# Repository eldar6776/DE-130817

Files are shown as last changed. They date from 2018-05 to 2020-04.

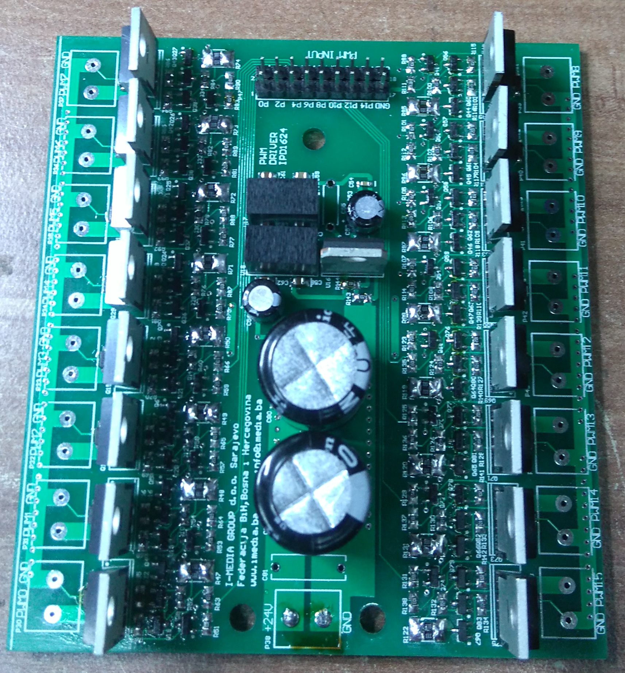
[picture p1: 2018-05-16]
RadioRxPwmImg3.JPG

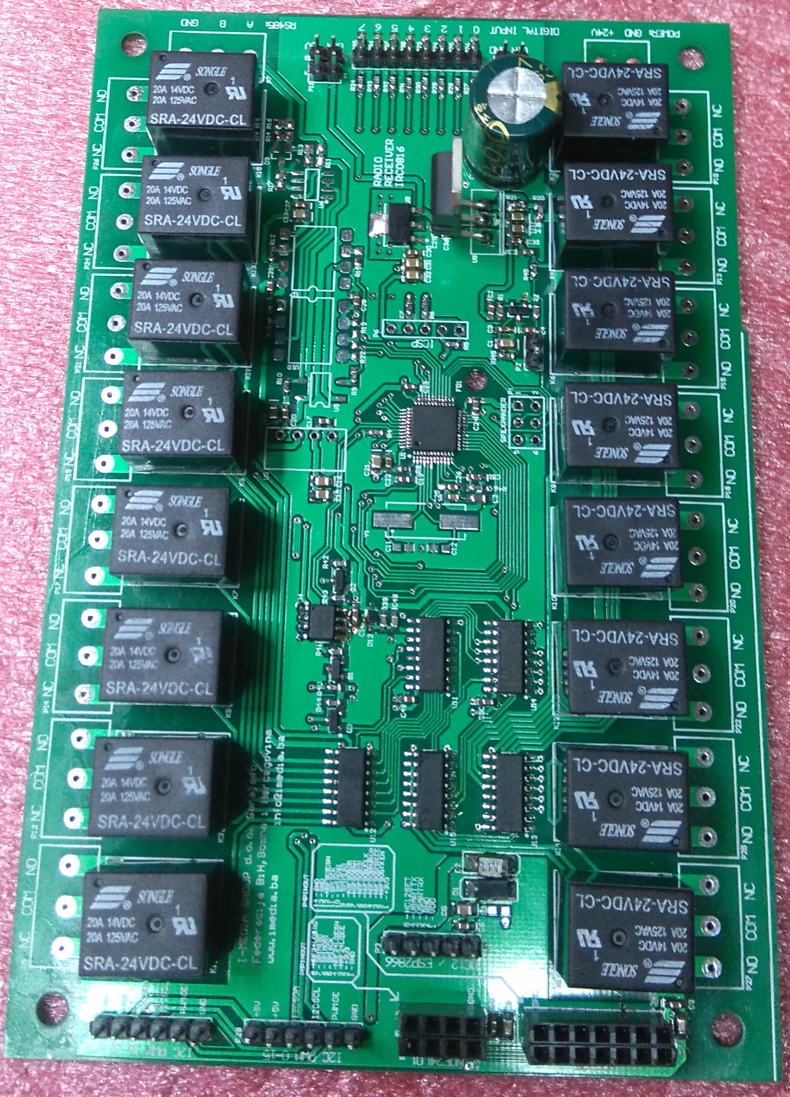
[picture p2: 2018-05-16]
RadioRxImg2.JPG

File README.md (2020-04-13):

# DE-130817
Two-Way Radio Link Receiver Modul

this is a receiver for DE-110817 transmitter, with a secure radio link to control the concrete pumps. 8 digital inputs are transmitted from the receiver to the transmitter, the PWM driver temperature of 65 degrees Celsius sends a warning to the transmitter, 80 degrees Celsius switches off and blocks the PWM and relay outputs except the oil pump and bypass valve controls. the supply voltage is also monitored. The 433MHz HC-12 radio modules are more than enough range for a stable radio link. if the transmitter does not confirm the transmitter packet longer than 500ms, the receiver switches off the outputs and an LED signal is activated on the transmitter.

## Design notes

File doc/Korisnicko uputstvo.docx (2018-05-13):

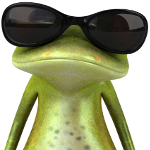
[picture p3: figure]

i MEDIA

__________________________________________________________________________________

Sistem radio kontrole pumpe za beton

Korisničko uputstvo

IRT0816 - Radio predajnik

8 analognih ulaza,

16 digitalnih ulaza,

8 led izlaza.

IRC0816 - Radio prijemnik

8 digitalnih ulaza,

16 relejnih izlaza,

16 PWM izlaza.

Posebne osobine:

- Podesiv indikator napona za većinu baterija ili akumulatora za napajanje predajnika: Nikal-Kadmium, suhi olovni akumulator, Litium-Ion, jednokratne alkalne baterije.
- Predupozorenje prazne baterije ispod 10% kapaciteta.
- Isključenje uređaja kod donjeg nivoa baterije što je ujedno i zaštita akumulatora od dubokog pražnjenja i oštećenja.
- Dvosmjerna radio komunikacija sa sigurnosnom funkcijom isključenja izlaza prijemnika kod prekida komunikacije >500 ms.
- Status prijemnika LED signalima na predajniku + stanje 8 digitalnih ulaza prijemnika koji se mogu koristiti za signalizaciju događaja sa prijemnika npr. min. nivou ulja, pregrijavanju, proradi zaštitnih uređaja, aktiviranju krajnjih ili sigurnosnih prekidača i sl.
- Stabilan izvor pozitivnog napona +3,3Vdc za referentni napon potenciometara spojenih na analogne ulaze.
- Zaštita PWM drivera od pregrijavanja sa signalom predupozorenja.
- RS485 interfejs za žičnu, backup, komunikaciju do 1km sa UTP, FTP, STP kablom za slučaj kvara ili smetnji radio komunikacije.

Fleksibilnost ugradnje:

- Jednostavno uspostavljanje optimalnog radio linka odabirom između 5 različitih radio modula i radnih frekvencija 315MHz, 433MHz, 868MHz, 915MHz, 2,4GHz, plug-and-play izmjenom bez dodatnih podešavanja za sigurnu radio kontrolu.
- Jednostavno podešavanje analognih ulaza za signale sa joystick potenciometara sa nulom na sredini klizača ili za signal potenciometara sa nulom signala na početku klizača
- Podesiva frekvencija PWM drivera za najoptimalniju kontrolu radnog uređaja sa što manjim gubicima i disipacijom temperature izlaznog PWM stepena.
- Mogućnost proširenja analognih/ digitalnih ulaza predajnika kao i pwm/relejnih izlaza prijemnika.
- Mogućnost ugradnje WiFi modula i kontrole prijemnika internet servisima tako da se modul može kristiti u Smart Home sistemu za on/off kontrolu 16~32 potrošača. PWM driver se bez ikakve preinake može koristiti za dimmer kontrolu 5~10 RGB ili 16~32 White LED nizova velike snage. Sa malim izmjenama, t.j. zamjenom tri komponente po kanalu, PWM driver se može transformisat u 16~32 kanalni DAC kojim se generišu kontrolni signali 0~10Vdc, a koji su industrijski standard i ulazni kontrolni signal kod mnogih LED dimmera

Karakteristike periferija:

- Signal na digitalnom ulazu prijemnika ili predajnika < 1Vdc je stanje logičke nule.
- Signal na digitalnom ulazu prijemnika ili predajnika > 2Vdc je stanje logičke jedinice.
- Maximalan pozitivni napon digitalnih ulaza prijemnika ili predajnika je < 30Vdc.
- Maksimalan pozitivni napon analognih ulaza predajnika je < 3,6Vdc.
- Signal na ulazu PWM drivera > 4Vdc postavlja izlaz PWM-a na visoki nivo (napon napajanja PWM drivera).
- Signal na ulazu PWM drivera < 3,5 Vdc postavlja izlaz PWM-a na niski nivo (GND PWM drivera).
- Izlaz PWM-a je N-MOSFET, zbog manjih gubitaka, u high-side switch spoju, t.j. kontrola pozitivnog napona. Upotrebljeni tip je maksimalnog radnog napona 100Vdc i 20A konstantne struje pri temperaturi kućišta do 100°C.
- Za temperature hladnjaka PWM drivera > 65°C aktivira se signal upozorenja na prijemniku.
- Temperatura hladnjaka PWM drivera > 80°C aktivira signal preopterećenja na prijemniku i aktivira zaštitnu funkciju koja isključuje sve izlaze prijemnika i onemogućava aktiviranje dok temperatura hladnjaka ne opadne ispod 65°C.
- Temperaturni senzor temperature hladnjaka PWM-a je NTC otpornik otpora 10K na temperaturi 25°C, na temperaturi 65°C je 2 K, a na temperaturi 80°C je 1,25 K.
- Na svim analognim ulazima su ugrađeni niskopropusni RC filteri ~150Hz koji eliminišu ili uveliko umanjuju smetnje nastale pomjeranjem klizača potenciometara koji su pred kraj radnog vijeka ili su već istrošeni.

Sadržaj uputstva:

1.0 Podešavanje i upotreba modula predajnika ................................... 6
2.0 Podešavanje i upotreba modula prijemnika.................................... 12
3.0 Pregled modula PWM drivera............................................................... 14
4.0 Električne sheme ......................................................................................... 17
5.0 Održavanje uređaja ................................................................................... 19
1. Podešavanje i upotreba modula predajnika :

raspored i namjena konektora na modulu radio predajnika

Kontrolni

taster

Konektor za

signalne LED

Konektor za

RS485 bus

Konektor za

napajanje

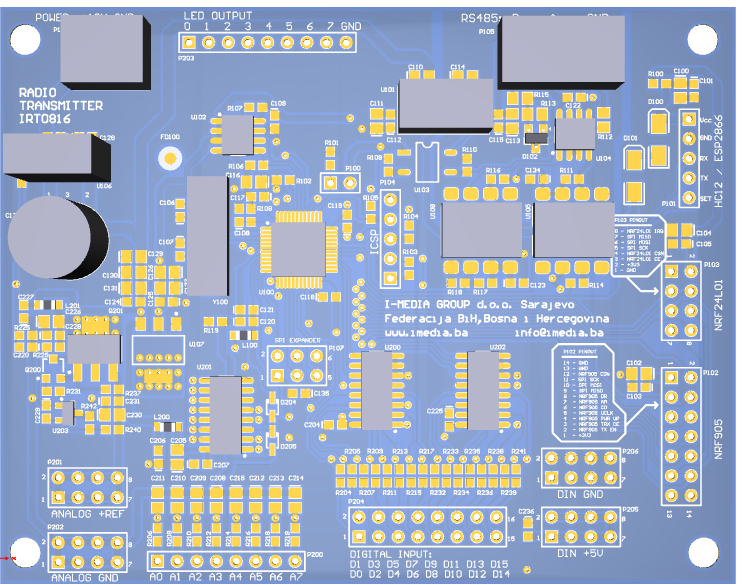
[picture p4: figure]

Konektor za modul proširenja

Konektor za

HC12 radio

modul i WiFi

Konektor za

NRF24L01

radio modul

Konektor za

NRF905 radio

modul

Masa za potenciometre

+3,3Vdc za

potenciometre

Analogni ulazi za potenciometre

Digitalni

ulazi

Masa za digitalne ulaze

+5Vdc za

digitalne ulaze

tabela napona standardnih ćelija

Tip ćelije/ napon | Olovna | Ni-Cd | Ni-MH | Li-ion
Napon ćelije (nominal.) | 2V | 1,2V | 1,2V | 3,7V
Napon pune ćelije | 2,40V | 1,45V | 1,41V | 4,20V
Napon prazne ćelije | 1,75V | 1,00V | 1,00V | 3,20~3,40V

  1.1 Način aktiviranja i izlaz iz funkcije podešavanja

Funkcija za podešavanje modula se aktivira tako da se pritisne kontrolni taster,

a zatim dok je taster pritisnut priključi napajanje predajnika. Sve statusne LED kratkim signalom označavaju da je funkcija aktivna. Nakon što je definisan parametar koji se podešava potrebno je kratko pritisnut kontrolni taster čime se nova vrijednost memoriše u eeprom i odmah je validna. Statusne LED sa tri kratka signala označavaju izlaz iz funkcije za podešavanje.

  1.2 Definisanje analognih ulaza

Kada je digitalni ulaz D0 spojen na +5Vdc i svi ostali digitalni ulazi su slobodni ili spojeni na masu, aktivirana funkcija podešavanja se odnosi na definisanje tipa signala na analognim ulazima. Analogne ulaze na koje će u toku rada uređaja biti spojen signal sa joystick potenciometra treba spojiti na 3,3Vdc, a analogne ulaze koji na koje će biti spojen signal sa standardnog potenciometra treba spojiti na masu. Nakon izlaza iz funkcije podešavanja definisani su analogni ulazi. Veoma je bitno da se ima u vidu da će sve promjene prvom konekcijom biti podešene i na prijemniku. Analogni ulaz predajnika na koji je spojen signal potenciometra joystick-a, na strani prijemnika kontroliše dva PWM izlaza koji su uvijek susjedni, a signal standardnog potenciometra kontroliše jedan PWM. Kada se promjeni definicija analognih ulaza treba i na strani prijemnika utvrditi novi raspored PWM izlaza.

  1.3 Podešavanje napona prazne baterije

Kada je digitalni ulaz D1 predajnika spojen na +5Vdc i svi ostali digitalni ulazi su slobodni ili spojeni na masu, aktivirana funkcija podešavanja se odnosi na definisanje napona prazne baterije. Napon napajanja treba podesiti na napon prazne baterij, a što se može izračunati prema „tabeli napona standardnih ćelija“, tako da se pomnoži broj članaka u bateriji za napajanja sa naponom prazne ćelije za korišteni tip. Najbolje je za napajanje koristiti podesivi izvor istosmjernog napona, a može se koristiti i ispražnjena baterij. Kada je napon definisan, kratko pritisnut kontrolni taster čime je izmjerena vrijednost memorisana kao donji prag napona baterije.

  1.4 Podešavanje napona pune baterije

Kada je digitalni ulaz D2 predajnika spojen na +5Vdc i svi ostali digitalni ulazi su slobodni ili spojeni na masu, aktivirana funkcija se odnosi na podešavanje napona pune baterije. Napon napajanja treba prije podesiti na napon pune baterije, a što se može izračunati prema „tabeli napona standardnih ćelija“, tako da se pomnoži broj članaka u bateriji za napajanja sa naponom pune ćelije za korišteni tip. Najbolje je za napajanje koristiti podesivi izvor istosmjernog napona, a može se koristiti i puna baterija. Kada je napon definisan, potrebno je kratko pritisnut kontrolni taster čime je izmjerena vrijednost memorisana kao napon pune baterije.

  1.5 Podešavanje frekvencije PWM izlaza 0 ~ 15

Kada je digitalni ulaz D3 predajnika spojen na +5Vdc i svi ostali digitalni ulazi su slobodni ili spojeni na masu, aktivirana je funkcija podešavanja frekvencije PWM signala za izlaze od 0 ~ 15. Signalom od 0 do 3,3Vdc na analognom ulazu A0 predajnika se podešava frekvencija PWM izlaza na prijemniku u rasponu od 24Hz do1526Hz. LED signali predstavljaju podešenu vrijednost i to za svaki LED koji svijetli konstantno frkvencija se uvećava za 200Hz, a trepćući signal označava uvećanje za 100Hz. Podešena frekvencija će biti podešena na prijemniku kod prve radio komunikacije sa predajnikom.

  1.6 Podešavanje frekvencije PWM izlaza 16 ~ 31

Kada je digitalni ulaz D4 predajnika spojen na +5Vdc i svi ostali digitalni ulazi su slobodni ili spojeni na masu, aktivirana je funkcija podešavanja frekvencije PWM signala za izlaze od 16 ~ 31. Signalom od 0 do 3,3Vdc na analognom ulazu A0 predajnika se podešava frekvencija PWM izlaza na prijemniku u rasponu od 24Hz do1526Hz. LED signali predstavljaju podešenu vrijednost i to za svaki LED koji svijetli konstantno frkvencija se uvećava za 200Hz, a trepćući signal označava uvećanje za 100Hz. Podešena frekvencija će biti podešena na prijemniku kod prve radio komunikacije sa predajnikom.

  1.7 Provjera statusa baterije

Kratkim pritiskom na kontrolni taster modula predajnika provjerava se status baterije prema LED signalima u rasponu od LED 0 za najmanji nivo do LED 7 za punu bateriju. Nakon 5 sekundi LED signali ponovo označavaju status prijemnika.

  1.8 Provjera statusa radio linka

Kratkim pritiskom na kontrolni taster modula predajnika za vrijeme provjere statusa baterije aktivira se provjera kvaliteta radio linka prema LED signalima u rasponu od LED 0 do LED 7. Ovaj mod ostaje aktivan do novog ciklusa napajanja

ili sledećeg pritiska na kontrolni taster nakon čega se ponovo LED signalima označava status prijemnika. Mjerenjem kvaliteta radio linka se mogu na vrijeme uočiti zone lošeg radio signala i izbjeći zastoji u radu mašine.

  1.9 Nuliranje analognih ulaza

Dužim pritiskom > 3s kontrolnog tastera modula predajnika, kada nije aktivna ni jedna druga funkcija podešavanja ili provjere, te otpuštanjem kontrolnog tastera, signali na analognim ulazima se definišu kao nulte pozicije potenciometara. Prije poziva ove funkcije potrebno je sve potenciometre dovesti u početne ili neutralne pozicije. Za potenciometre joystick-a napon signala u neutralnom položaju je idealno 1,65Vdc, a za ostale potenciometre je napon signala u početnoj poziciji 0Vdc, mada se ovom funkcijom mogu definisati nulte pozicije potenciometara i u bilo kojem drugom položaju npr. kada je signal sa potrošenog potenciometra nestabilan (šušti) na početku hoda, može se nula pomjeriti na dio klizača odakle je signal stabilan. Sve vrijednosti ispod nulte pozicije klizača su jednake nuli signala na izlazu PWM-a.

  1.10 RS485 interfejs za serijsku - backup konekciju

Komunikaciju između predajnika i prijemnika je moguće ostvariti povezivanjem RS485 interfejsa predajnika i prijemnika uvrnutom paricom dužine do 1000 m. Brzina serijske komunikacije je 9600 bps, a format 8-N-1. Ovim interfejsom se korištenjem seta komandi mogu podesiti svi parametri prijemnika i predajnika. Potreban je serijski teminal softver (npr. realterm) i konverter USB/RS485.

  1.11 HC-12 Radio modul

Radna frekvencija je u opsegu 433 – 473MHz podjeljena na 100 kanala. Uz izlaznu snagu od max. 100mW (20dB) i brzinu prenosa do 5000 bps na otvorenom prostoru moguće je ostvariti dvosmjernu komunikaciju do 1000 m. Ako je par ovih radio modula priključen na konektore P3 prijemnika i P101 predajnika, u toku inicijalizacije softvera prvi su odabir za radio link.

  1.12 NRF24L01+PA+LNA Radio modul

Radna frekvencija je 2,4GHz. Izlazna snaga predajnika je >100mW (>20dB), brzina prenosa do 2MB. Na otvorenom prostoru moguće je ostvariti dvosmjernu komunikaciju preko 700 m, brzine prijenosa 1MB. Ako je par ovih radio modula priključen na konektore P5 prijemnika i P103 predajnika, u toku inicijalizacije softvera drugi su odabir za radio link.

  1.13 NRF905 Radio modul

Radne frekvencije su u tri banda 433/868/915MHz. Izlazna snaga predajnika je 10mW (10dB) , brzina prenosa do 50 kbps. Na otvorenom prostoru moguće je ostvariti dvosmjernu komunikaciju do 300 m. Ako je par ovih radio modula priključen na konektore P4 prijemnika i P102 predajnika, u toku inicijalizacije softvera treći su odabir za radio link uspostavljen na bandu 433MHz.

  1.14 LED signalizacija stanja digitalnih ulaza prijemnika i greške

Konektor P203 modula predajnika omogućava monitoring raznih statusa prijemnika i predajnika sa 8 LED dioda koje se spajaju anodama na pinove 1 do 8 konektora P203, a sve katode se spajaju na zajednički pin 9. Serijski otpornici su ugrađeni na modulu i nije ih potrebno dodavati eksterno. Struja izlaza za LED diode sa padom napona od 2V je ~3mA, a za LED diode sa padom napona 3V je ~1mA, što treba uzeti u obzir kada se uređaj napaja baterijama.

Stanje aktivnog digitalnog ulaza na prijemniku se signalizira konstantno svjetlećom LED na predajniku sa istim brojem (LED 0 za digitalni ulaz DIN 0) i obratno, LED je neaktivna kada je digitalni ulaz neaktivan.

Signalizacija greške se označava sa tri kratke promjene stanja LED signala i pauzom od tri sekunde. To znači ako LED svijetli zato što je taj digitalni ulaz aktivan, onda će emitovanje svjetla biti tri puta kratko prekinuto i nakon svake tri sekunde ponovo, a ako je LED bila neaktivna onda će tri puta kratko zasvjetliti i nakon tri sekunde pauze ponavljati ovaj signal.

Značenje signaliziranih grešaka:

LED 0 - napon baterije za napajanje predajnika ispod 10% - upozorenje

LED 1 - baterija za napajanje predajnika prazna - isključenje

LED 2 - greška modula I2C PWM kontrolera - isključenje

LED 3 - temperatura hladnjaka PWM izlaza veća od 65°C - upozorenje

LED 4 - temperatura hladnjaka PWM izlaza veća od 80°C - isključenje

LED 5 - greška NTC temistora za mjerenje temperature PWM - isključenje

LED 6 - prekid radio linka > 500 ms - isključenje

LED 7 - prekid u napajanju prijemnika - isključenje

  1.15 Spajanje analognih ulaza

Svi analogni ulazi su za napone od 0 do 3,3Vdc (!!! NE 5Vdc), za što je na PCB-u modula preajnika obezbjeđen stabilan referentni izvor napona na konektoru P201. Potenciometri na ulazu se spajaju na konektore P200, P201 i P202.

ANALOG +REF (P201)

A0; A1....A7 (P200)

ANALOG GND (P202)

  1.16 Spajanje digitalnih ulaza

Svi digitalni ulazi su predviđeni za ulazni napon do 30Vdc. Na PCB-u modula predajnika se nalaze konektori P204; P205; P206 za dva načina spajanje digitalnih ulaza: sa eksternim izvorom i internim izvorom. Kod spajanja sa internim izvorom, na konektoru P205 je obezbjeđen izvor +5Vdc za beznaponski kontakt koji se drugim izvodom spaja na digitalne ulaze na konektoru P204. Ako se koristi eksterni izvor, minus pol izvora se spaja na DIN GND konektor P206 modula, a pozitivan pol izvora se spaja na digitalne ulaze na konektoru P204. Stanje digitalnog ulaza u odnosu na napon izvora je opisano u dijelu „Karakteristike periferija“.

spajanje digitalnog ulaza za internim izvorom

DIN +5V(P205) D0; D1.....D15 (P204)

spajanje digitalnog ulaza za eksternim izvorom

0~30V D0; D1.....D15 (P204)

GND DIN GND(P206)

  1.17 Spajanje kontrolnog tastera

Za korištenje funkcija: „provjera statusa baterije, provjera statusa radio linka, nuliranje analognih ulaza “, kao i za podešavanja modula predajnika potreban je spoj kontrolnog tastera. Ovaj taster bi trebao biti zaštićen od slučajnog pritiska u toku rada sa predajnikom zbog mogućnosti neželjenog aktiviranja funkcije „nuliranje analognih ulaza“ , a samim tim i zastoja u radu dok se ova funcija ponovo provede.

spajanje kontrolnog tastera

P100/1 P100/2

2. Podešavanje i upotreba modula prijemnika :

raspored i namjena konektora na modulu radio predajnika

LOOP VENTIL

RELEJ 15

RELEJ 9

RELEJ 10

RELEJ 11

RELEJ 12

RELEJ 13

RELEJ 13

RELEJ 14

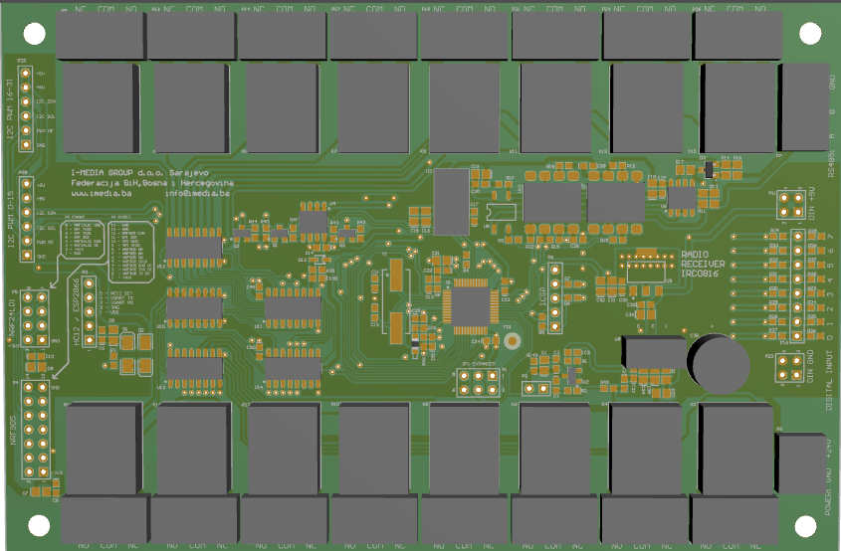
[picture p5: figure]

Konektor NTC senzora

Masa za digitalne ulaze

Konektor za

napajanje

RELEJ 7

RELEJ 6

RELEJ 5

RELEJ 8

RELEJ 4

RELEJ 3

RELEJ 2

RELEJ 1

Konektor za

NRF905

radio modul

Konektor za

PWM kontroler 2

modul

Konektor za

RS485 bus

Digitalni

ulazi

+5Vdc za

digitalne ulaze

Konektor za

NRF24L01

radio modul

Konektor za

PWM kontroler 1

modul

Konektor za

HC12 radio

modul i WiFi

  2.1 NTC senzor temperature hladnjaka PWM izlaza

Tip NTC senzora je pisan u dijelu „Karakteristike periferija“ i korišten je veoma dostupan i najčešće korišteni tip 10K na 25°C. Kada se koristi potrebno je tijelo NTC termistora sa malo termoprovodne paste učvrstiti na hladnjak PWM izlaza i dvožičnim provodnikom spojiti na P2 modula prijemnika. Ovaj provodnik je potrebno odvojiti od provodnika PWM i relejnih izlaza koji su izvor smetnji.

Monitoring teperature hladnjaka PWM drajvera se može isključiti postavljanjem jumpera (kratak spoj) na konektor P2 u slučaju npr. neispravnog NTC termistora ili kada se ne koristi PWM driver.

  2.2 Spajanje digitalnih ulaza

Svi digitalni ulazi su predviđeni za ulazni napon do 30Vdc. Na PCB-u modula prijemnika se nalaze konektori P11; P16; P23 za dva načina spajanje digitalnih ulaza: sa eksternim izvorom i internim izvorom. Kod spajanja sa internim izvorom, na konektoru P11 je obezbjeđen izvor +5Vdc za beznaponski kontakt koji se drugim izvodom spaja na digitalne ulaze na konektoru P16. Ako se koristi eksterni izvor, minus pol izvora se spaja na DIN GND konektor P23 modula, a pozitivan pol izvora se spaja na digitalne ulaze na konektoru P16. Stanje digitalnog ulaza u odnosu na napon izvora je opisano u dijelu „Karakteristike periferija“.

spajanje digitalnog ulaza za internim izvorom

DIN +5V(P11) D0; D1.....D7 (P16)

spajanje digitalnog ulaza za eksternim izvorom

0~30V D0; D1.....D7 (P16)

GND DIN GND(P23)

  2.3 Spajanje PWM kontrolera

Na modul prijemnika je moguće priključiti dva 16 kanalna PWM kontrolera za generisanje PWM signala 0-5Vdc. Kada se koristi drugi PWM kontroler, na prijemniku je potrebno ugraditi modul proširenja analognih ulaza. Rad modula prijemnika je moguć sa i bez modula PWM kontrolera. Ako je modul PWM kontrolera priključen na PCB prijemnika, nakon priključenja napona, softver će registrovati modul i u slučaju kvara ili isključenja u toku rada prijavit će grešku modula te isključiti sve izlaze prijemnika. Ako modul PWM kontrolera nije bio priključen kod uključenja napajanja prijemnika, PWM funkcija izlaza se ne koristi te prijemnik služi kao on/off rejeni kontroler.

Pregled modula PWM drivera :

PCB i raspored komponenti PWM Drivera IPD1624

PWM

izlaz 5

PWM

izlaz 4

PWM

izlaz 3

PWM

izlaz 2

PWM

izlaz 1

PWM

izlaz 0

PWM

izlaz 7

PWM

izlaz 6

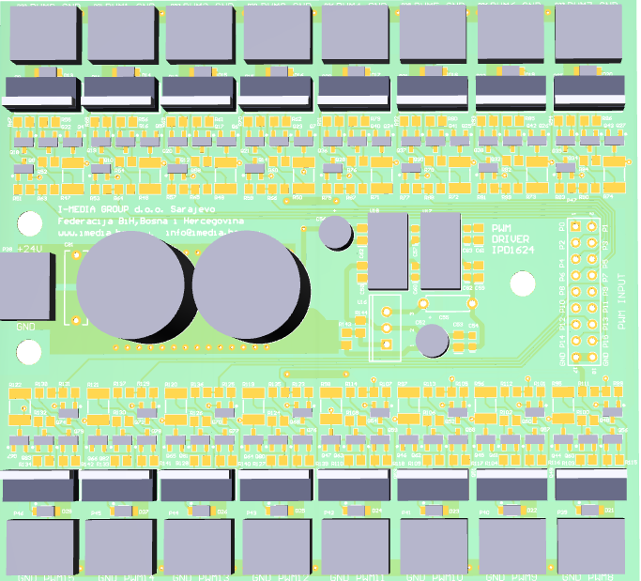
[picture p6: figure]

PWM

izlaz 9

PWM

izlaz 10

PWM

izlaz 11

PWM

izlaz 12

PWM

izlaz 13

PWM

izlaz 14

PWM

izlaz 15

Napajanje

PWM

drivera

PWM

ulazi

0 ~ 15

PWM

izlaz 8

PWM driver IPD1624 je predviđen kao univerzalan PWM izlazni stepen za širok opseg opterećenja i radnih napona, te kao takav nema implementiranu prekostrujnu zaštitu i koju je potrebno izvesti eksterno prema opterećenju koje se spaja na izlaz. Zaštita se može izvesti serijskom vezom staklenog rastalnog osigurača (tromog T ili brzog F) i priključenog opterećenja t.j. radnog uređaja (proporcionalni elektro ventil, servo pozicioner, aktuator), a što treba provjeriti u specifikaciji za taj uređaj. Primjer spoja zaštite je skiciran ispod.

SF52 (5A, 100V)

ventil

T2A

PWM GND

izlaz osigurač

Niti na jedan od PWM izlaza drivera se ne smije priključivati izvor napajanja bilo da je PWM driver priključen na napajanje ili da je napajanje isključeno. Ovo bi za posljedicu imalo pregorijevanje gate otpornika izlaznog MOSFET-a, zaštitne zener diode ili pnp gate-driver tranzistora.

Ukoliko je potreban bilo kakav paralelan rad PWM drivera i nekog drugog kontrolnog sklopa, potrebno je ili napraviti preklopnik ručna komanda – radio komada ili na izlaz PWM-a koji je u paralelnom spoju sa dodatnom kontrolom ugraditi diodu za blokadu pozitivnog napona sa izlaza prema unutrašnjem sklopu PWM drivera. Dioda treba biti dimenzionisana prema struji priključenog opterećenja. Treba voditi računa da je pad napona na diodi oko 0,5 V što uz veću struju opterećenja od npr. 2A daje disipaciju od 1W, tako da je potrebno pobrinuti se za odvođenje viška toplote sa diode na hladnjak .

spoj za preklopnik ručna komanda – radio komada

SF52 (5A, 100V)

PWM

T2A

izlaz

ventil

GND

Ručna

komanda

relej

Odabir

kontrole

spoj za blokadu pozitivnog napona sa ručne kontrole prema PWM driveru

MBRF20100CT SF52 (5A, 100V)

ventil

T2A

PWM

izlaz

GND

Ručna

komanda

Na sva induktivna opterećenja kontrolisana PWM driverom koja nemaju ugrađen snubber, obavezno je ugraditi flyback diodu bar duplo veće struje od struje kontrolisanog induktiviteta i bar duplo većeg reversnog napona od napona napajanja PWM drivera. Bez eliminisanja smetnji koje nastaju kod isključenja napajanja induktivitetu, moguća su spontana, nekontrolisana uključenja izlaza PWM drivera kao i nekontrolisani reseti mikrokontrolera.

spoj flyback - zaštitne diode na induktivno opterećenje (elektroventil 2A, 24Vdc)

SF52 (5A, 100V)

T3,15A

ventil

PWM GND

izlaz

Električne sheme :

spajanje modula PWM kontrolera, PWM izlaza i radio modula prijemnika

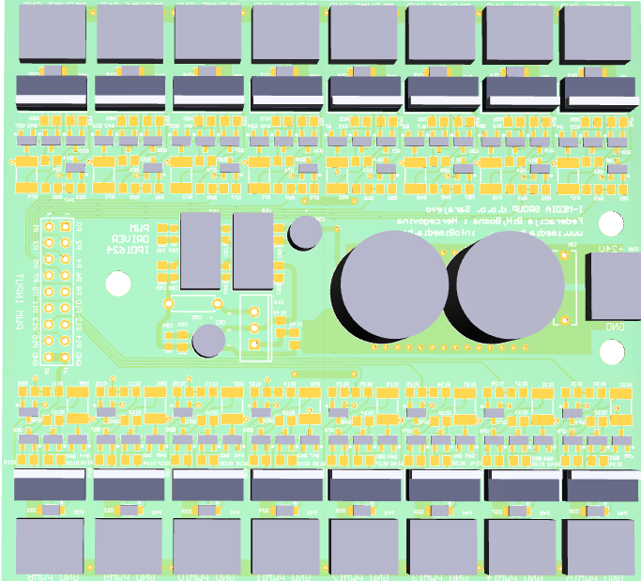
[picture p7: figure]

HC12

radio modul

vcc

PWM kontroler

!!! Kod povezivanja modula obrati pažnju na crveni marker kabla.

spajanje radio modula predajnika

HC12

radio modul

vcc

!!! Kod povezivanja modula obrati pažnju na crveni marker kabla.

Održavanje uređaja:

Ukoliko je signal sa potenciometra do te mjere nestabilan da prolazi kroz RC filter analognih ulaza, može se (za prvu pomoć) između signala sa klizača potenciometra i mase spojiti kondenzator 10 ~47 uF/10V pazeći da se negativni pol kondenzatora spoji na masu, a pozitivni na klizač. Veći kapacitet kondenzatora ima za rezultat veću stabilnost signala ali ujedno i sporiji odziv na promjene položaja potenciometra. Naročito je važno kašnjenje do nule signala t.j. kada se klizač brzo pomjeri u nultu poziciju, signal će kasniti i još neko vrijeme ostati aktivan dok ne postigne nultu vrijednost, pa je najbolje potenciometre koji uzrokuju smetnje zamjeniti novim.

BETTON PLANET © 2007–2018 I-Media Group d.o.o SarajevoPage 15

IRT0816 – Radio transmiter & IRC0816 – Radio receiver

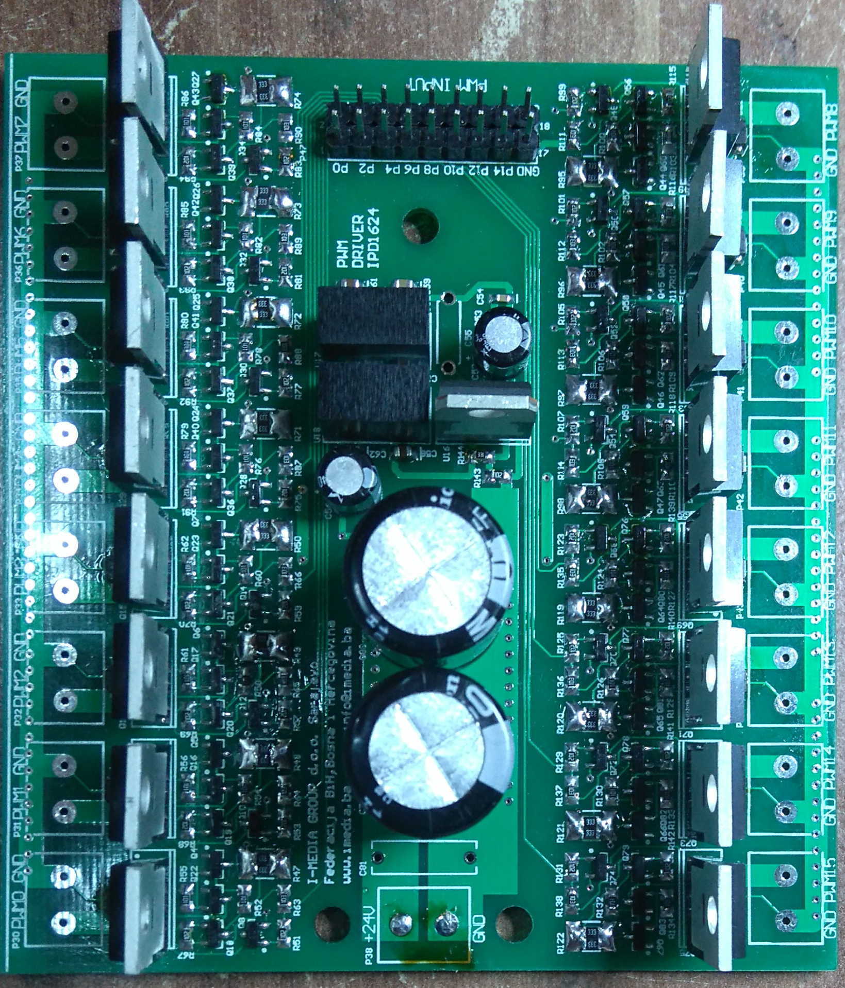
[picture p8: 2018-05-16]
RadioRxPwmImg1.JPG

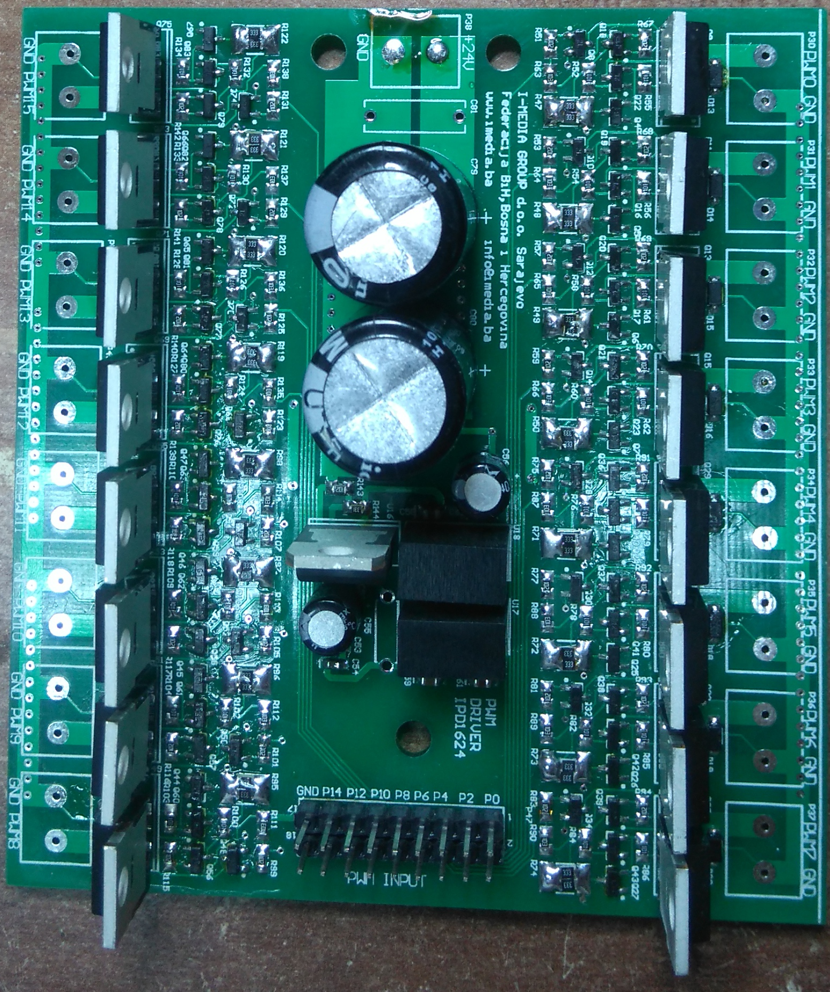
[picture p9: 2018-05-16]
RadioRxPwmImg4.JPG

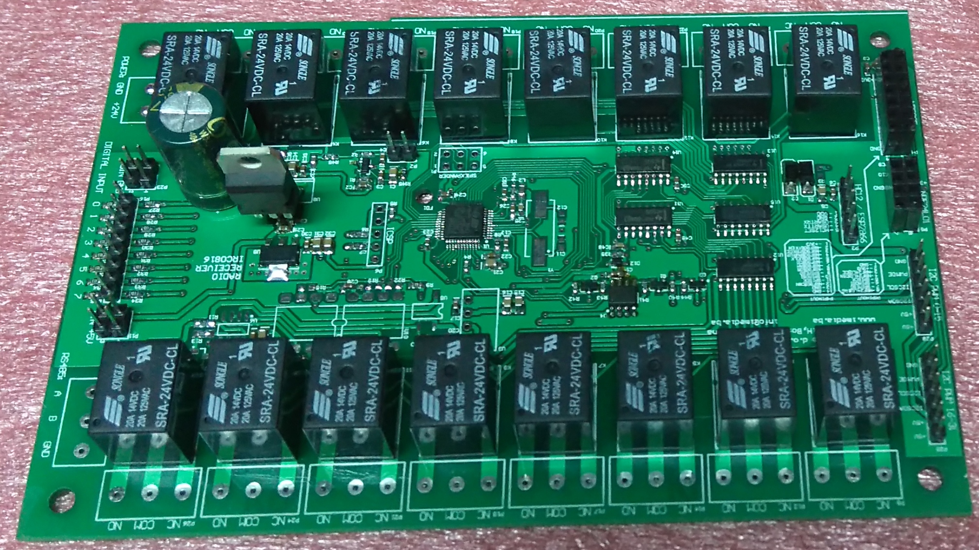
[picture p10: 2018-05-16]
RadioRxImg1.JPG

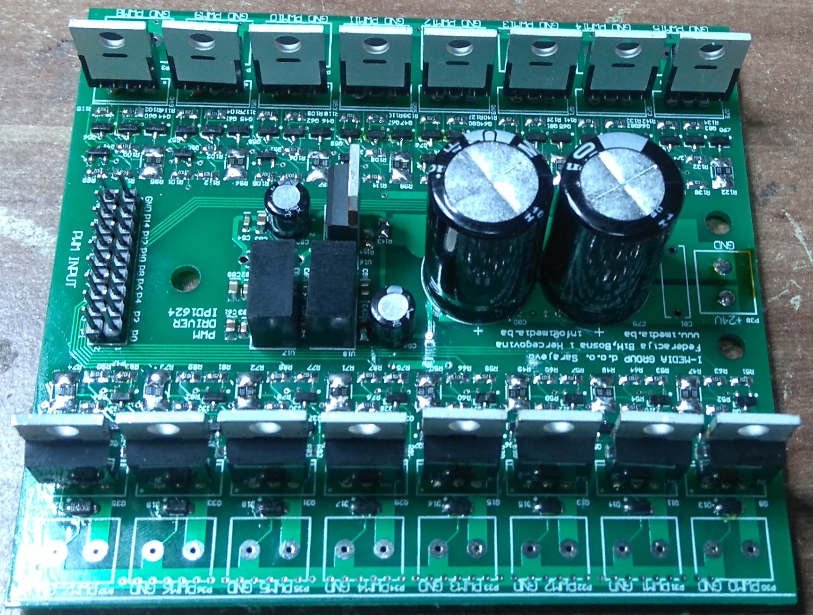
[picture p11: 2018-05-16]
RadioRxPwmImg2.JPG

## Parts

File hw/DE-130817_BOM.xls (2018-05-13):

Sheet: BOM Report
Bill of Materials |  |  | Cuc & Com
Source Data From: |  | DE-130817.PrjPcb
Project: |  | DE-130817.PrjPcb
Variant: |  | None
Creation Date: | 13.5.2018. | 14:30:54
Print Date: | 43233 | 43233.60602
Footprint | Comment | LibRef | Designator | Description | Quantity
0805 | 10uF | C0805 | C1, C5, C7, C9, C15, C16, C18, C19, C21, C31, C32, C34, C35, C36, C53, C58, C59, C61, C62 | Ceramic Chip Capacitor - Standard | 19
0603 | 100nF | C0603 | C2, C3, C4, C6, C8, C10, C13, C14, C17, C20, C22, C23, C24, C26, C27, C28, C29, C30, C33, C37, C39, C40, C41, C42, C43, C44, C45, C46, C47, C49, C50, C51, C54, C57, C60, C82, C83 | Ceramic Chip Capacitor - Standard | 37
0603 | 22pF | C0603 | C11, C12 | Ceramic Chip Capacitor - Standard | 2
0603 | 1uF | C0603 | C25, C48 | Ceramic Chip Capacitor - Standard | 2
CAPPR5-10x16 | 1000uF | EKA00DD410D00 | C38 | Aluminum Electrolytic Capacitor, Radial Style with Long Leads: 1000uF, 16V | 1
CAPPR2-5X11 | EKA00AA247F00 | EKA00AA247F00 | C52, C56 | Aluminum Electrolytic Capacitor, Radial Style with Long Leads: 47uF, 35V | 2
VP52-2.5 | VP52BY104 | VP52BY104 | C55 | Dipped Radial Multilayer Ceramic Capacitor X7R: 100nF | 1
CAPPR7.5-16X35.5 | EKA00JL422H00 | EKA00JL422H00 | C79, C80 | Aluminum Electrolytic Capacitor, Radial Style with Long Leads: 2200uF, 50V | 2
VP60-3.6 | VP60BA104FB | VP60BA104FB | C81 | Dipped Radial Multilayer Ceramic Capacitor COG (NPO): 100nF, 100V | 1
SMA | 1N4001 | 1N4001 | D1, D2 | Schottky Rectifier | 2
SOT23_3L | SM712 | 824022 | D3 | TVS Diode WE-TVS-Standard, VRWM=5.0V | 1
ONSC-SOD-323-2-477-02_V | 3V3 | MM3Z33VT1G | D4, D5, D6, D7, D8, D9, D10, D11 | Zener Voltage Regulator, 300 mW, 2-Pin SOD-323, Pb-Free, Tape and Reel | 8
SOD323 | 1N4148 | BAS321 | D12 | General-purpose Diode | 1
ONSC-SOD-123-2-425-04_V | SZMMSZ12T1G | SZMMSZ12T1G | D13, D14, D15, D16, D17, D18, D19, D20, D21, D22, D23, D24, D25, D26, D27, D28 | Zener Voltage Regulator, 500 mW, 2-Pin SOD-123, Pb-Free, Tape and Reel | 16
SRA-5VDC-CL | SRA-5VDC-CL | SRA-5VDC-CL | K1, K2, K3, K4, K5, K6, K7, K8, K9, K10, K11, K12, K13, K14, K15, K16 | SPDT PCB relay 5Vdc coil | 16
SMD-0805 | 120R | 74279202 | L2 | SMD EMI Suppression Ferrite Bead WE-CBF, Z = 120 Ohm | 1
HDR2X3 | SPI2_EXP | Header 3X2 | P1 | Header, 3-Pin, Dual row | 1
HDR1X2 | 10K NTC | Header 2 | P2 | Header, 2-Pin | 1
HDR1X5 | HC12_RADIO | Header 5 | P3 | Header, 5-Pin | 1
HDR2X7 | nRF905 | Header 7X2 | P4 | Header, 7-Pin, Dual row | 1
HDR2X4 | NRF24L01 | Header 4X2 | P5 | Header, 4-Pin, Dual row | 1
HDR1X5 | ULINK_ICSP | Header 5 | P6 | Header, 5-Pin | 1
TERMINAL BLOK 3 | TERMINAL BLOK 3 | TERMINAL BLOK 3 | P7, P9, P10, P12, P13, P14, P15, P17, P18, P19, P20, P21, P22, P24, P25, P26, P27 | 3 pinski terminal blok konektor | 17
TERMINAL BLOK 2 | TERMINAL BLOK 2 | TERMINAL BLOK 2 | P8, P30, P31, P32, P33, P34, P35, P36, P37, P38, P39, P40, P41, P42, P43, P44, P45, P46 | 2 pinski terminal blok | 18
HDR2X2 | DIN_VCC | Header 2X2 | P11 | Header, 2-Pin, Dual row | 1
HDR1X8 | DIGITAL_INPUT | Header 8 | P16 | Header, 8-Pin | 1
HDR2X2 | DIN_VSS | Header 2X2 | P23 | Header, 2-Pin, Dual row | 1
HDR1X6 | I2C_PWM_0_15 | Header 6 | P28 | Header, 6-Pin | 1
HDR1X6 | I2C_PWM_16_31 | Header 6 | P29 | Header, 6-Pin | 1
HDR2X9 | Header 9X2 | Header 9X2 | P47 | Header, 9-Pin, Dual row | 1
ONSC-SOT-23-3-318-08_V | BSS138LT1 | BSS138LT1 | Q1, Q2, Q3 | Power MOSFET, 200 mA, 50 V, N-Channel, 3-Pin SOT-23, Tape and Reel | 3
SOT23_N | MMBT5551 | BC817 | Q4, Q5, Q6, Q7, Q24, Q25, Q26, Q27, Q44, Q45, Q46, Q47, Q64, Q65, Q66, Q67 | NPN General-purpose Transistor | 16
SOT23_N | MMBT5401 | BC807 | Q8, Q10, Q12, Q14, Q16, Q17, Q22, Q23, Q28, Q30, Q32, Q34, Q40, Q41, Q42, Q43, Q48, Q50, Q52, Q54, Q60, Q61, Q62, Q63, Q68, Q70, Q72, Q74, Q80, Q81, Q82, Q83 | PNP General-purpose Transistor | 32
TO-220AB | IRF540N | IRF540N | Q9, Q11, Q13, Q15, Q29, Q31, Q33, Q35, Q49, Q51, Q53, Q55, Q69, Q71, Q73, Q75 | HEXFET Power MOSFET | 16
SOT23_N | BSS123 | BSS123 | Q18, Q19, Q20, Q21, Q36, Q37, Q38, Q39, Q56, Q57, Q58, Q59, Q76, Q77, Q78, Q79 | N-channel Enhancement Mode Vertical D-MOSFET | 16
ERA-0603 | 820R | ERAV | R1 | Metal Film Thermosensitive Chip Resistor, 0.56 Ohm to 10k Ohm Range, 5% Tolerance, 0603 Size, 0.063 W | 1
ERA-0603 | 2K2 | ERAV | R2, R41, R43 | Metal Film Thermosensitive Chip Resistor, 0.56 Ohm to 10k Ohm Range, 5% Tolerance, 0603 Size, 0.063 W | 3
ERA-0603 | NF | ERAV | R3 | Metal Film Thermosensitive Chip Resistor, 0.56 Ohm to 10k Ohm Range, 5% Tolerance, 0603 Size, 0.063 W | 1
ERA-0603 | 10K | ERA3Y, ERA3Y, ERAV, ERAV, ERAV, ERAV, ERAV, ERAV, ERAV, ERAV, ERAV, ERAV, ERAV, ERAV, ERAV, ERAV, ERAV, ERAV, ERAV, ERAV, ERAV | R4, R5, R23, R24, R25, R26, R27, R28, R29, R30, R31, R32, R33, R34, R35, R36, R37, R38, R40, R42, R44 | Rectangular Thick Film Chip Resistor, 10 Ohm to 330k Ohm Range, 0.1% and 0.5% Tolerance, 0603 Size, 0.063 W, Rectangular Thick Film Chip Resistor, 10 Ohm to 330k Ohm Range, 0.1% and 0.5% Tolerance, 0603 Size, 0.063 W, Metal Film Thermosensitive Chip Resis | 21
ERA-0603 | 100R | ERA3Y | R6, R7 | Rectangular Thick Film Chip Resistor, 10 Ohm to 330k Ohm Range, 0.1% and 0.5% Tolerance, 0603 Size, 0.063 W | 2
ERA-0603 | 0R | ERA3Y, ERAV | R8, R145 | Rectangular Thick Film Chip Resistor, 10 Ohm to 330k Ohm Range, 0.1% and 0.5% Tolerance, 0603 Size, 0.063 W, Metal Film Thermosensitive Chip Resistor, 0.56 Ohm to 10k Ohm Range, 5% Tolerance, 0603 Size, 0.063 W | 2
ERA-0603 | 330R | ERAV, ERA3Y, ERAV | R9, R15, R18 | Metal Film Thermosensitive Chip Resistor, 0.56 Ohm to 10k Ohm Range, 5% Tolerance, 0603 Size, 0.063 W, Rectangular Thick Film Chip Resistor, 10 Ohm to 330k Ohm Range, 0.1% and 0.5% Tolerance, 0603 Size, 0.063 W, Metal Film Thermosensitive Chip Resistor, 0 | 3
ERA-0603 | 470R | ERAV | R10, R12 | Metal Film Thermosensitive Chip Resistor, 0.56 Ohm to 10k Ohm Range, 5% Tolerance, 0603 Size, 0.063 W | 2
ERA-0805 | 820R | ERA6Y | R11, R17 | Rectangular Thick Film Chip Resistor, 10 Ohm to 1M Ohm Range, 0.1% and 0.5% Tolerance, 0805 Size, 0.1 W | 2
ERA-0805 | 10R | ERA6Y | R13, R16 | Rectangular Thick Film Chip Resistor, 10 Ohm to 1M Ohm Range, 0.1% and 0.5% Tolerance, 0805 Size, 0.1 W | 2
ERA-0805 | 120R | ERA6Y | R14 | Rectangular Thick Film Chip Resistor, 10 Ohm to 1M Ohm Range, 0.1% and 0.5% Tolerance, 0805 Size, 0.1 W | 1
ERA-0603 | 510R | ERAV | R19 | Metal Film Thermosensitive Chip Resistor, 0.56 Ohm to 10k Ohm Range, 5% Tolerance, 0603 Size, 0.063 W | 1
ERA-0805 | 1K | ERA6Y | R20, R51, R53, R57, R59, R67, R68, R69, R70, R75, R77, R81, R83, R91, R92, R93, R94, R99, R101, R105, R107, R115, R116, R117, R118, R123, R125, R129, R131, R139, R140, R141, R142 | Rectangular Thick Film Chip Resistor, 10 Ohm to 1M Ohm Range, 0.1% and 0.5% Tolerance, 0805 Size, 0.1 W | 33
ERA-0805 | 330R | ERA6Y | R21 | Rectangular Thick Film Chip Resistor, 10 Ohm to 1M Ohm Range, 0.1% and 0.5% Tolerance, 0805 Size, 0.1 W | 1
ERA-0603 | 1K | ERAV | R22 | Metal Film Thermosensitive Chip Resistor, 0.56 Ohm to 10k Ohm Range, 5% Tolerance, 0603 Size, 0.063 W | 1
ERA-0603 | 100K | ERAV | R39 | Metal Film Thermosensitive Chip Resistor, 0.56 Ohm to 10k Ohm Range, 5% Tolerance, 0603 Size, 0.063 W | 1
ERA-0603 | 330K | ERAV | R45 | Metal Film Thermosensitive Chip Resistor, 0.56 Ohm to 10k Ohm Range, 5% Tolerance, 0603 Size, 0.063 W | 1
ERA-0603 | 39K | ERAV | R46 | Metal Film Thermosensitive Chip Resistor, 0.56 Ohm to 10k Ohm Range, 5% Tolerance, 0603 Size, 0.063 W | 1
12-1812 | 10K | ERJ12 | R47, R48, R49, R50, R71, R72, R73, R74, R95, R96, R97, R98, R119, R120, R121, R122 | Thick Film Chip Resistor, 1 Ohm to 10M Ohm Range, 5% Tolerance, 1812 Size, 0.5 W | 16
ERA-0805 | 100R | ERA6Y | R52, R54, R55, R56, R58, R60, R61, R62, R76, R78, R79, R80, R82, R84, R85, R86, R100, R102, R103, R104, R106, R108, R109, R110, R124, R126, R127, R128, R130, R132, R133, R134 | Rectangular Thick Film Chip Resistor, 10 Ohm to 1M Ohm Range, 0.1% and 0.5% Tolerance, 0805 Size, 0.1 W | 32
ERA-0805 | 10K | ERA6Y | R63, R64, R65, R66, R87, R88, R89, R90, R111, R112, R113, R114, R135, R136, R137, R138 | Rectangular Thick Film Chip Resistor, 10 Ohm to 1M Ohm Range, 0.1% and 0.5% Tolerance, 0805 Size, 0.1 W | 16
STM-LQFP48_N | STM32F103C8T6 | STM32F103C8T6 | U1 | ARM Cortex-M3 32-bit MCU, 64 KB Flash, 20 KB Internal RAM, 37 I/Os, 48-pin LQFP, -40 to 85 degC, Tray | 1
SOT23-3_N | TL431CL3T | TL431CL3T | U2 | Programmable Voltage Reference, 2.5 to 36V, 3-Pin SOT23-3, Tape and Reel | 1
B0505S-1W | B0505S/D-1W | B0505S/D | U3 | 1W isolated dc dc converter | 1
SOIC-SN8_N | AT24C1024 | 24AA64/SN | U4 | 64Kbit, 400kHz, 1.7V, I2C Serial EEPROM, 8-Pin SOIC 150mil, Commercial Temperature | 1
SOP4 | PS2501L | PS2501L optocoupler | U5 | 4-Pin Phototransistor Optocoupler | 1
D008_L | SN75176BD | SN75176BD | U6 | Differential Bus Transceiver | 1
SMD-8 | 6N137 | 6N137 | U7, U10 | High CMR, High Speed TTL Compatibile Optocoupler | 2
221A-06 | LM317MT | LM317MT | U8 | Three-Terminal Adjustable Output Positive Voltage Regulator | 1
ZZ311 | REG1117-3.3 | REG1117-3.3 | U9 | 800mA and 1A Low Dropout Positive Regulator 2.85V, 3.3V, 5V, and Adjustable | 1
751B-05_N | MC74HC595AD | MC74HC595AD | U11, U14 | 8-Bit Serial-Input/Serial or Prallel-Output Shift Register with Latched 3-State Outputs | 2
SO16_N | ULN2003D | ULN2003D | U12, U13, U15 | Seven Darlington Array | 3
TO220 | STEP DOWN BUCK | 7805 replacement switcher modul | U16 | Positive Voltage Regulator, 5V, 3-Pin TO-220 | 1
B0505S-1W | B0512S/D-1W | B0505S/D | U17, U18 | 1W isolated dc dc converter | 2
HC49/4H_SMX | 8MHz | HC49/4H_SMX | Y1 | Surface Mount Quartz Crystal | 1
 |  |  |  |  | 404
Approved |  | Notes

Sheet: Project Information
Project Full Path | F:\SkyDrive\OtvoreniProjekti\SuperBeton\hw\DE-130817\DE-130817.PrjPcb
Project Filename | DE-130817.PrjPcb
Variant Name | None
Data-Source Filename | DE-130817.PrjPcb
Data-Source Full Path | F:\SkyDrive\OtvoreniProjekti\SuperBeton\hw\DE-130817\DE-130817.PrjPcb
Title | Cuc & Com
Total Quantity | 404
Report Time | 14:30:54
Report Date | 13.5.2018.
Report Date & Tine | 13.5.2018. 14:30:54
Output Name | Bill of Materials
Output Type | BOM_PartType
Output Generator Name | BOM
Output Generator Description | Bill of Materials

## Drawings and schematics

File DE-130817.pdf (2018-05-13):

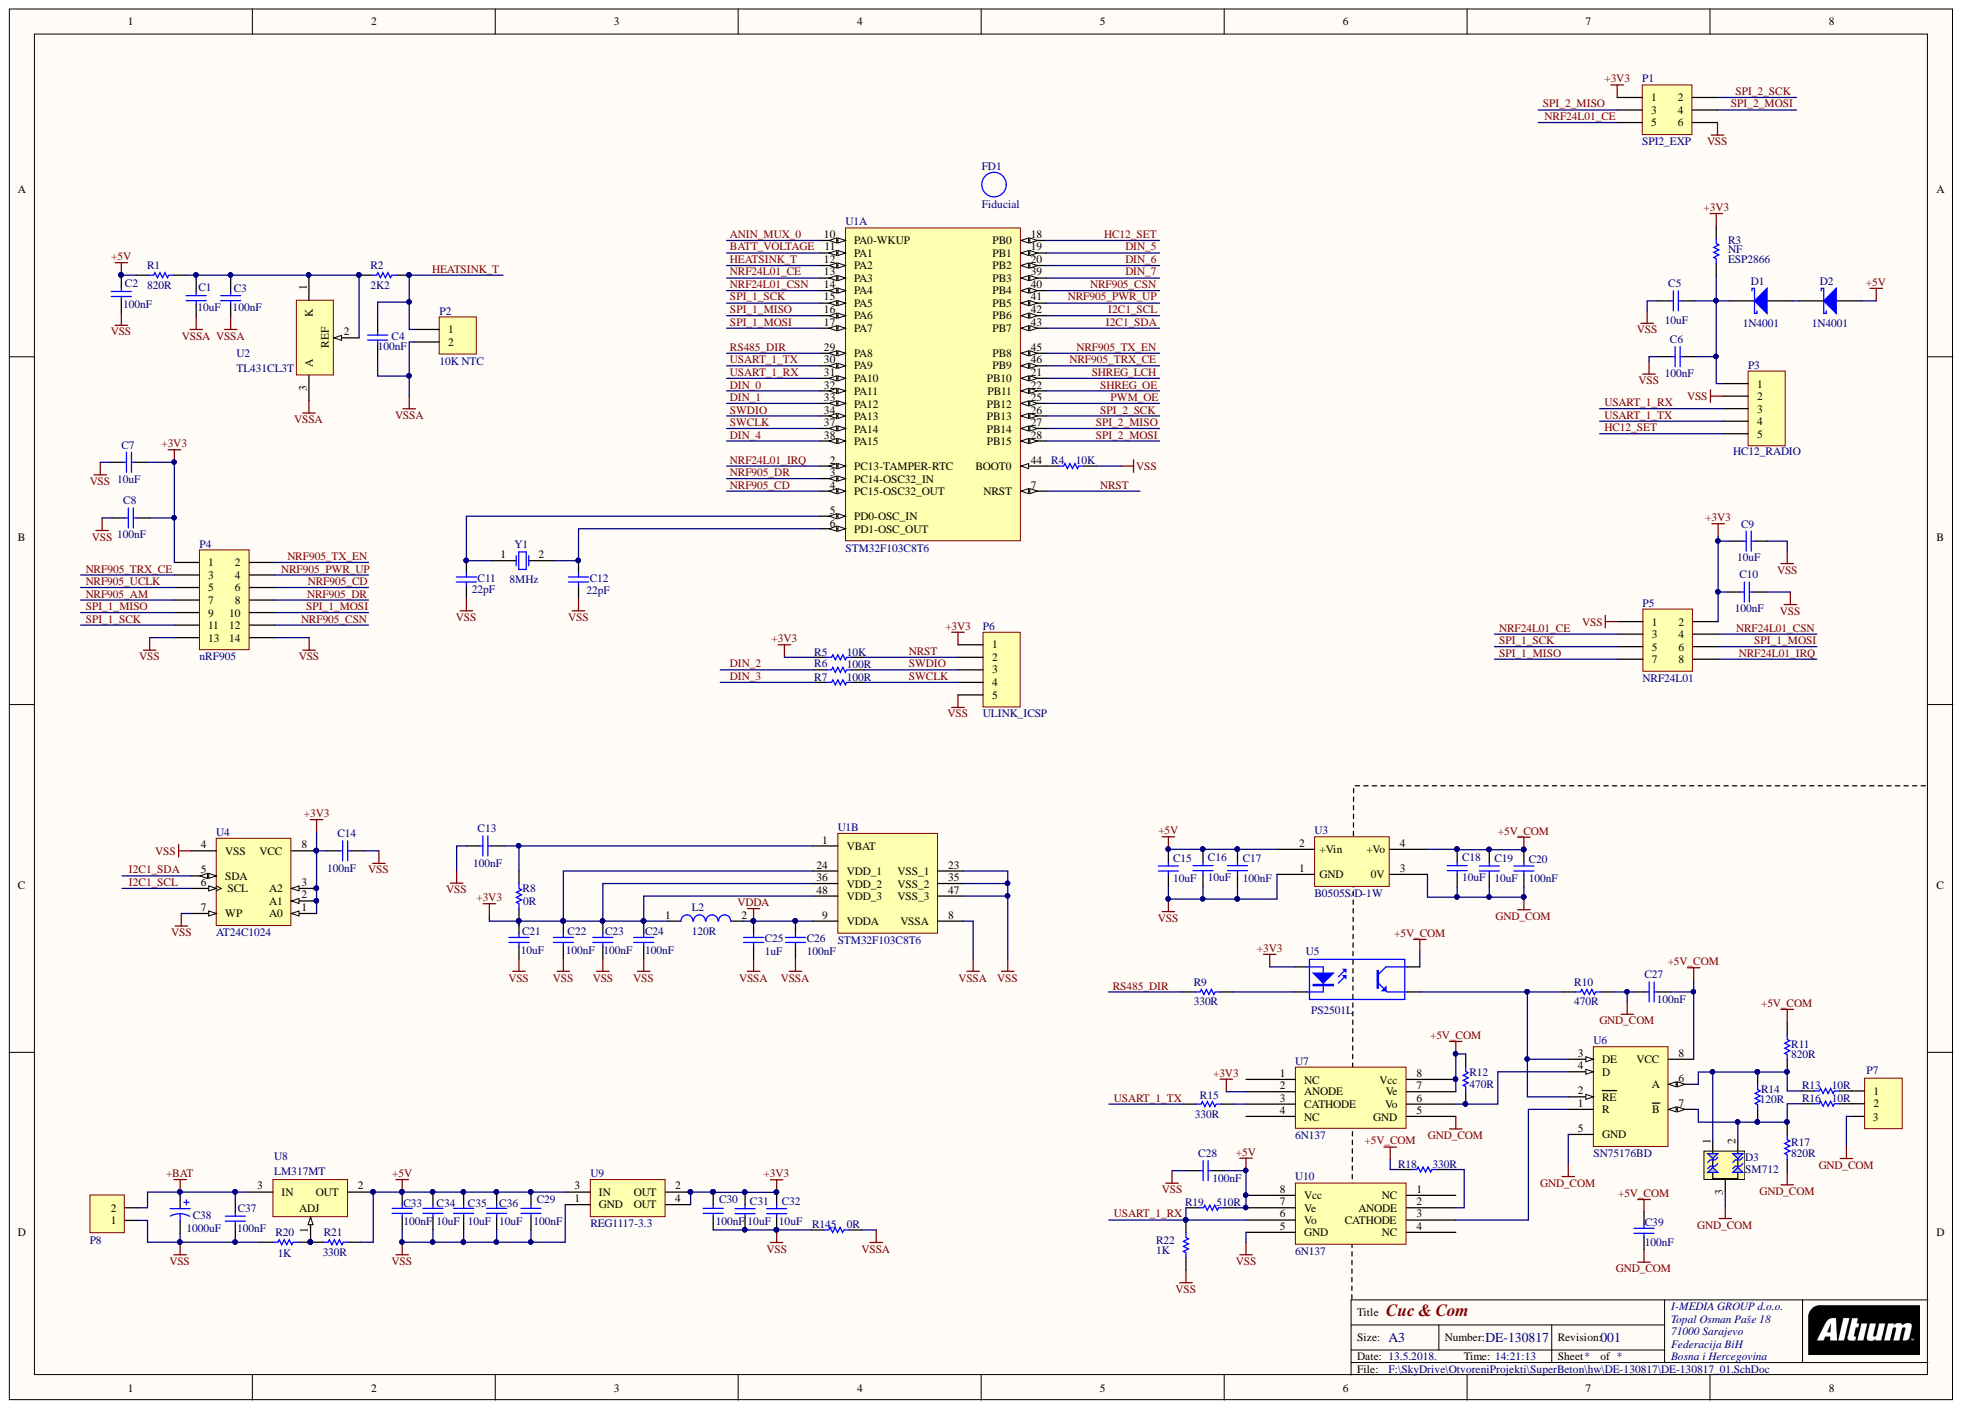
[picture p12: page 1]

Cuc & Com Title | I-MEDIA GROUP d.o.o. Topal Osman Paše 18 71000 Sarajevo Federacija BiH Bosna i Hercegovina

Size: A3 | Number: DE-130817 | Revision: 001
Date: 13.5.2018. Time: 14:21:13 | | Sheet * of *

F:\SkyDrive\OtvoreniProjekti\SuperBeton\hw\DE-130817\DE-130817_01.SchDoc

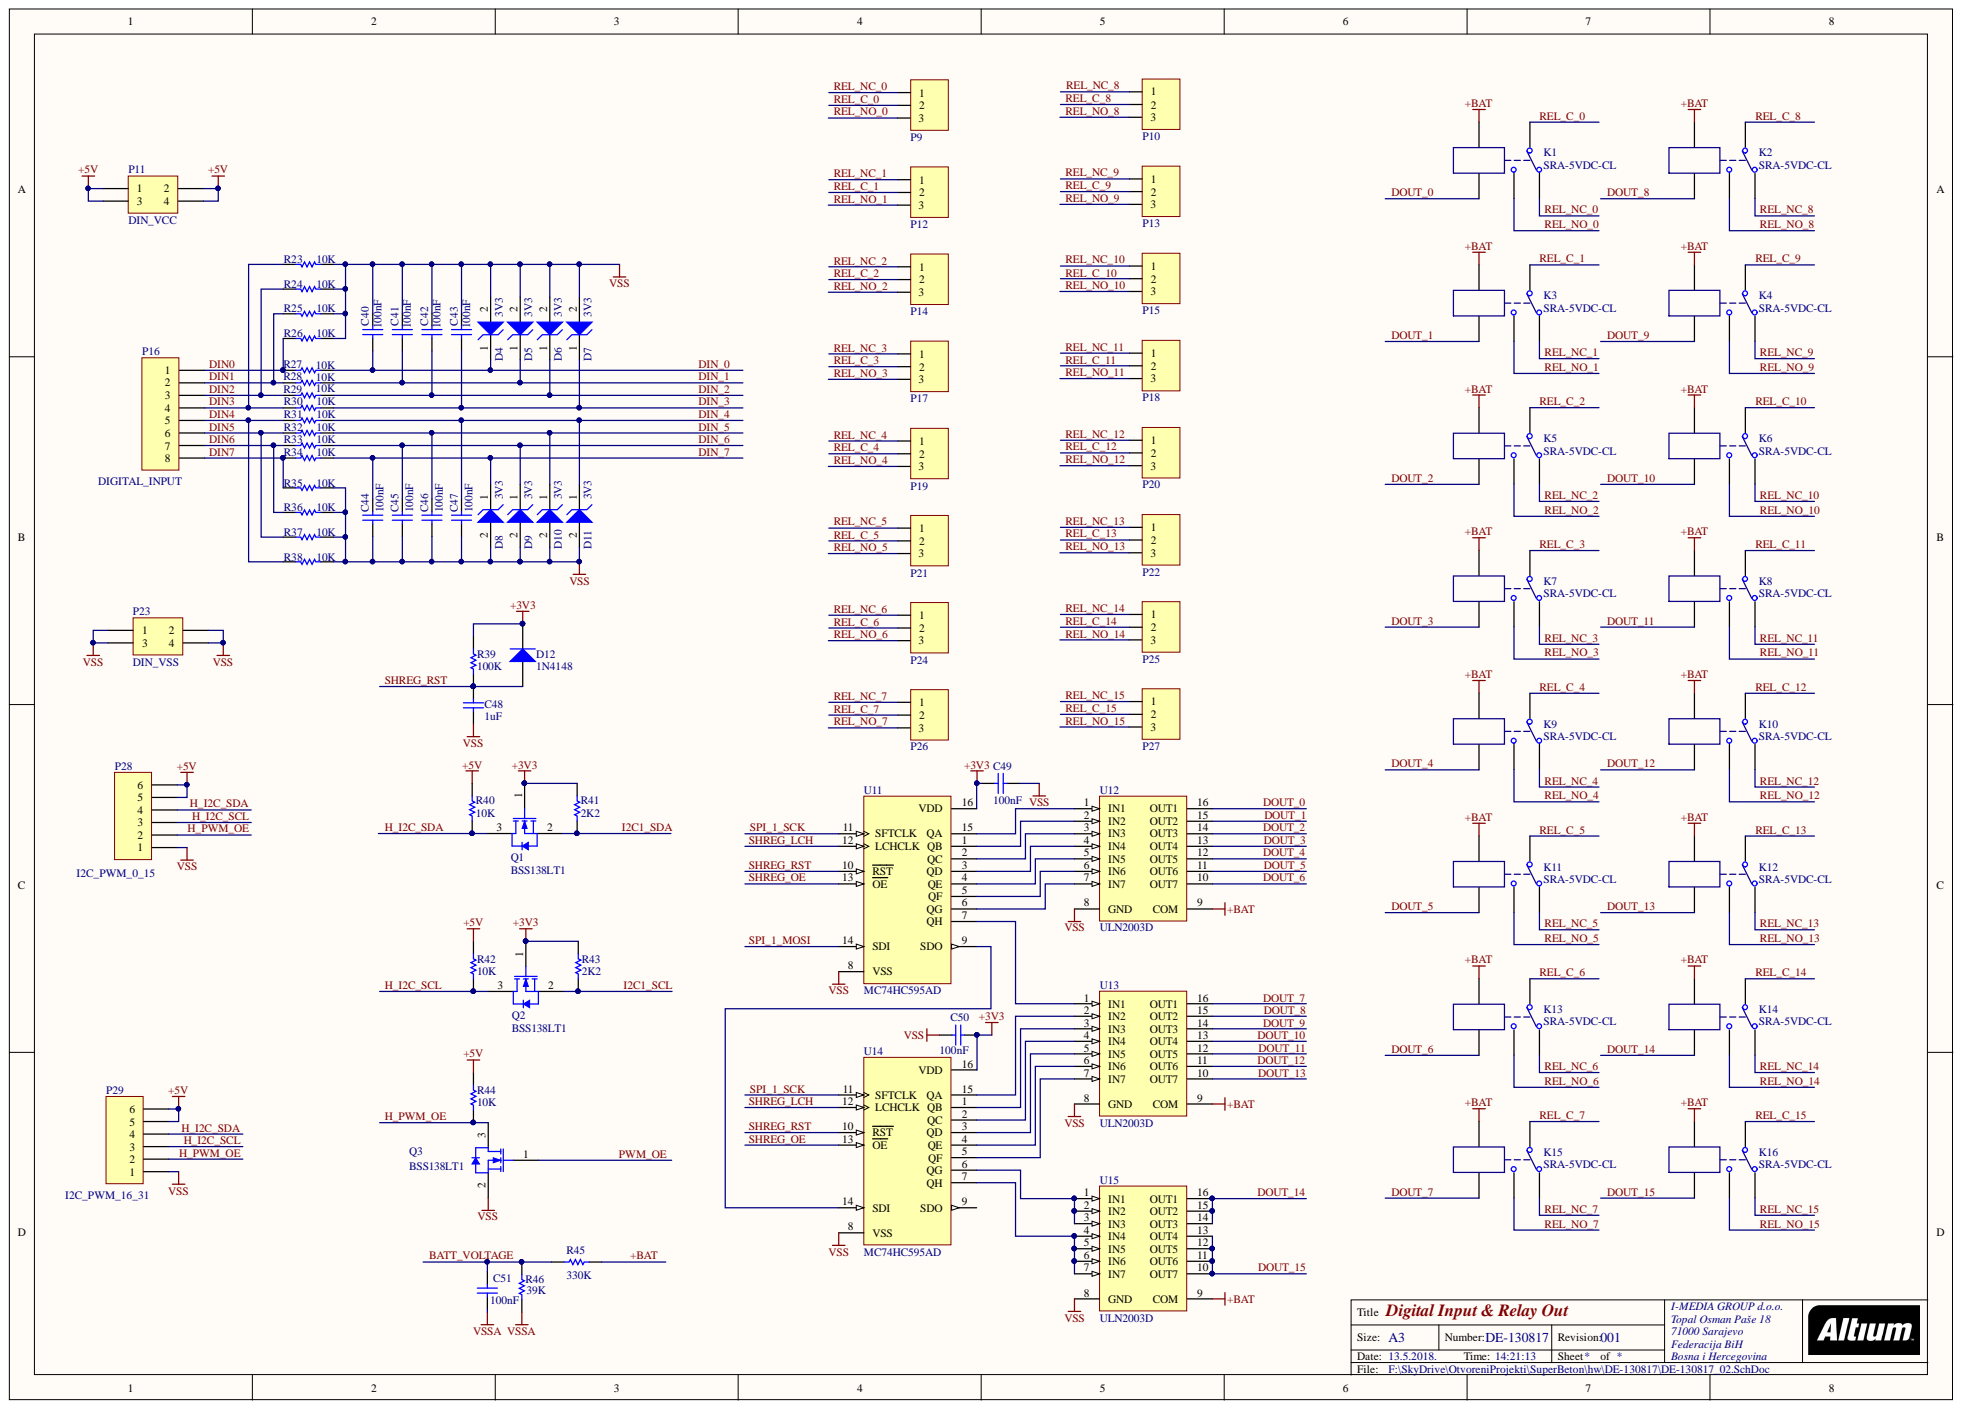
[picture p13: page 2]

6 | 1 1 D O U T_5
7 | D O U T_6

D igital Inpu t & Re lay O u t Ti t l e | I -MEDIA GR O UP d.o.o. Topal O s man P a še 18 71000 Sarajevo Federacija BiH Bosna i Hercegovina

Size: A | Number : D E-130817 | Revi s ion: 001

Ti me: | | Sheet of

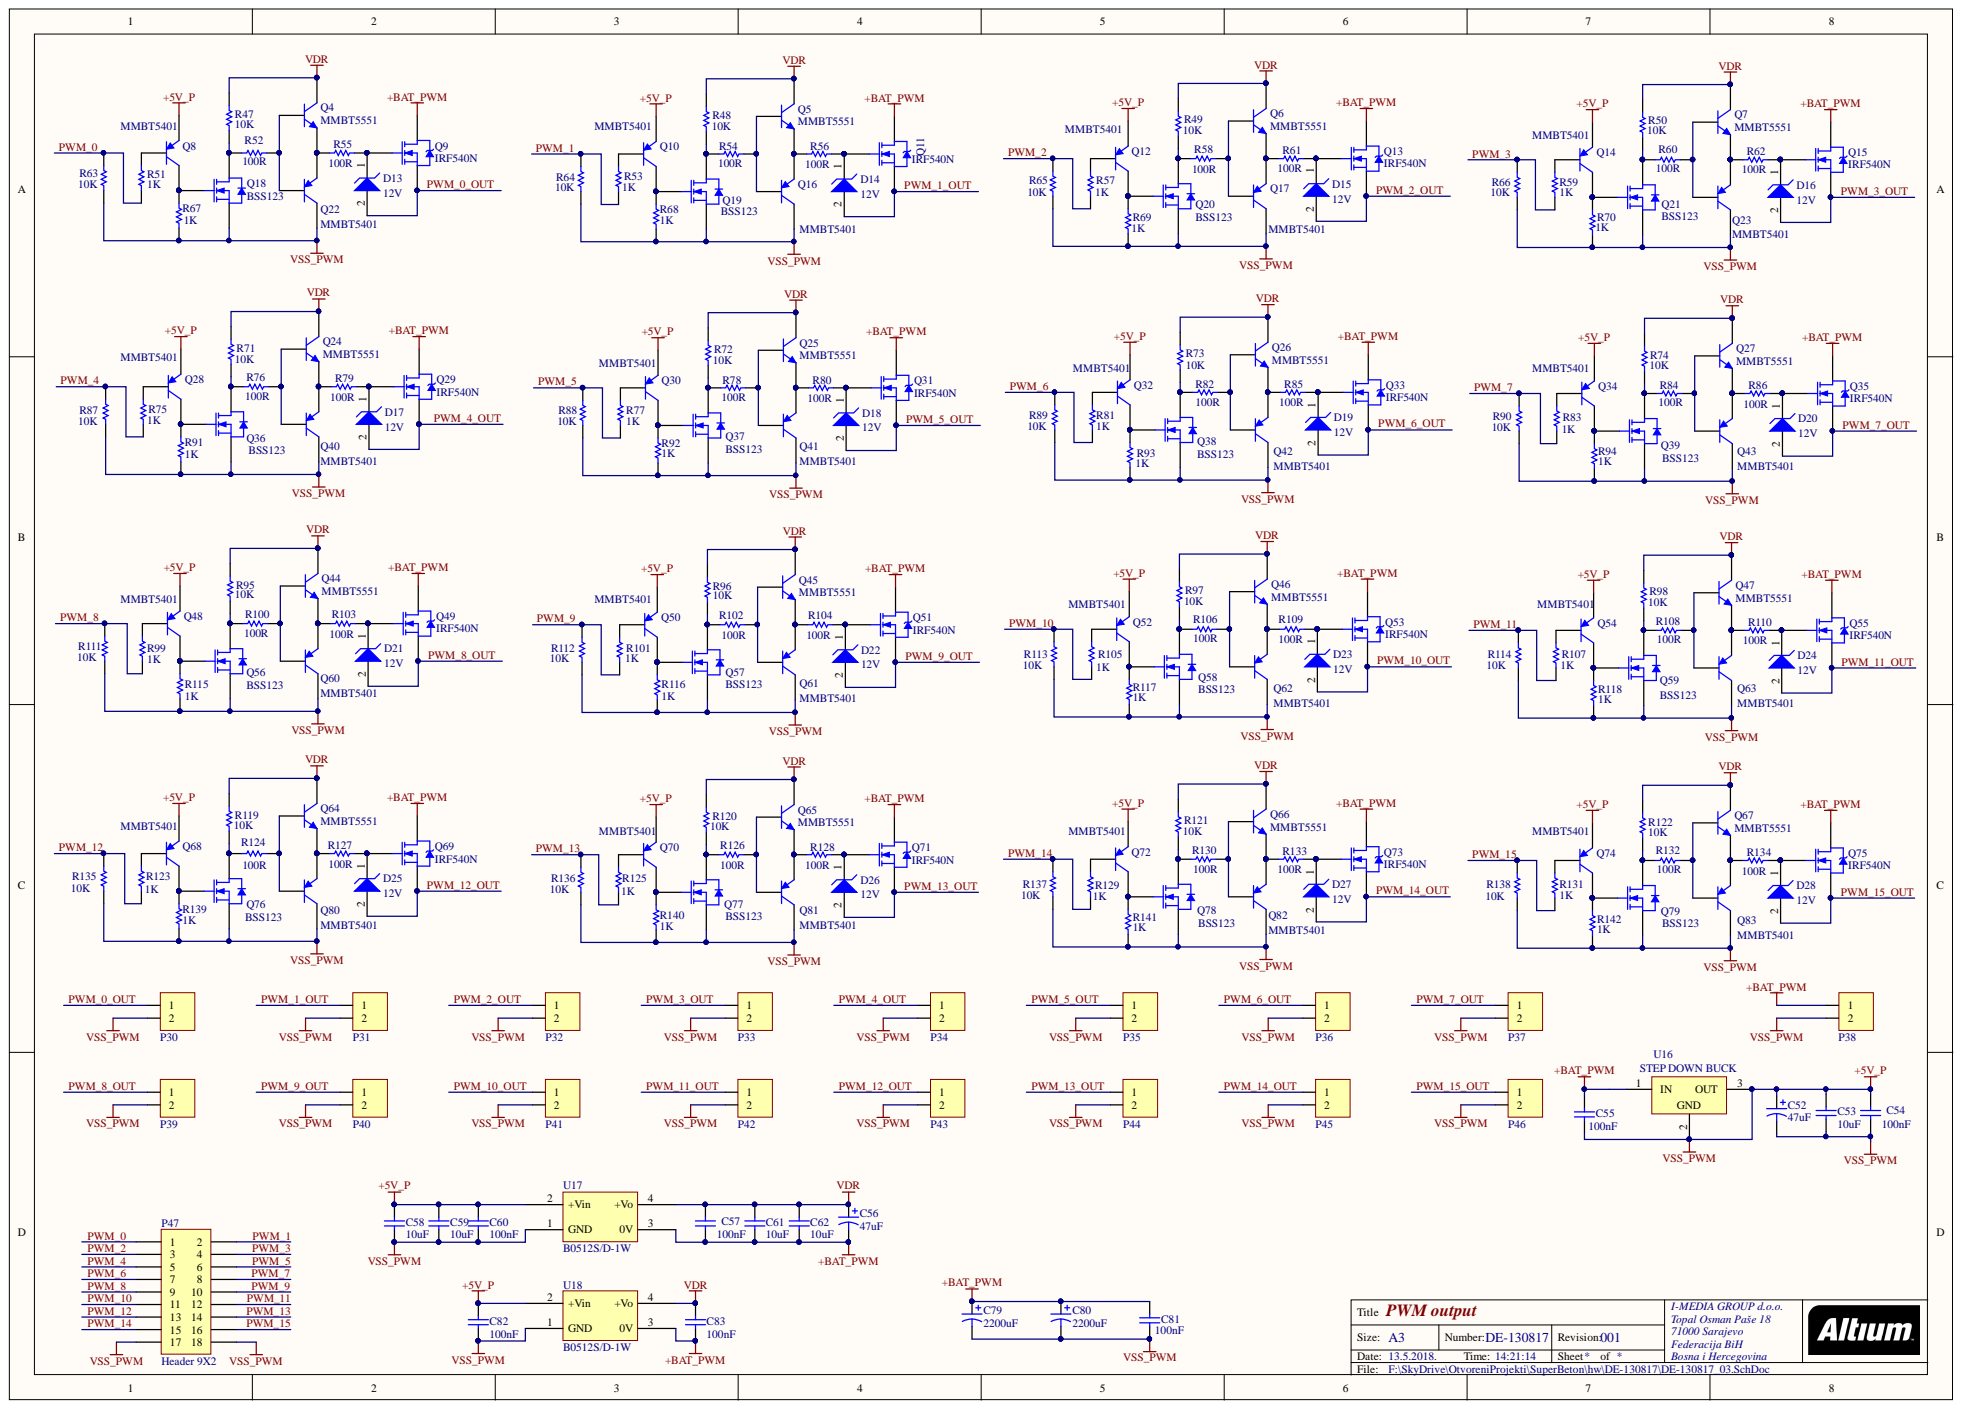
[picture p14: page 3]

F:\SkyDrive\OtvoreniProjekti\SuperBeton\hw\DE-130817\DE-130817_03.SchDoc

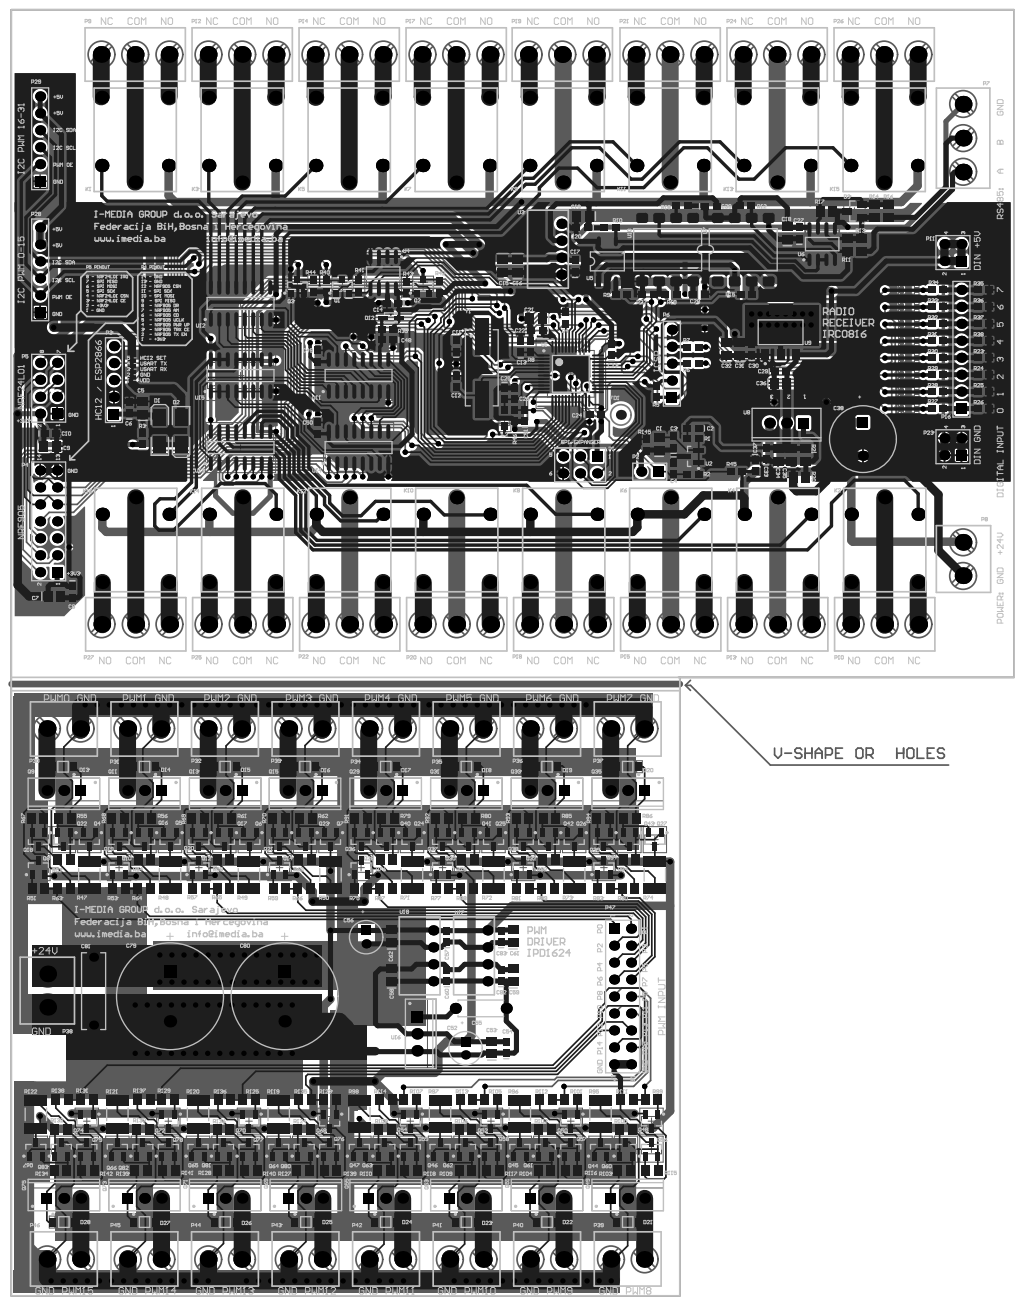
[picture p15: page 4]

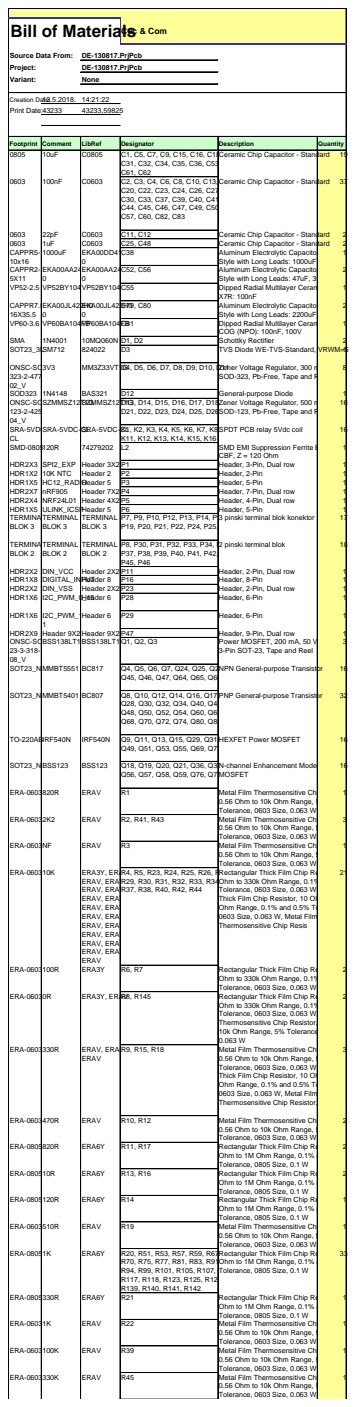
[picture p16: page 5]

Bill of MaterialsCuc & Com

Footprint | Comment | LibRef | Designator | Description | Quantity

Style with Long Leads: 1000uF, 16V

Style with Long Leads: 47uF, 35V

Style with Long Leads: 2200uF, 50V

SOD-323, Pb-Free, Tape and Reel

Zener Voltage Regulator, 500 mW, 2-Pin
SOD-123, Pb-Free, Tape and Reel

3-Pin SOT-23, Tape and Reel

N-channel Enhancement Mode Vertical D-
MOSFET

0.56 Ohm to 10k Ohm Range, 5%
Tolerance, 0603 Size, 0.063 W

Rectangular Thick Film Chip Resistor, 10
Ohm to 330k Ohm Range, 0.1% and 0.5%
Tolerance, 0603 Size, 0.063 W, Rectangular
Thick Film Chip Resistor, 10 Ohm to 330k
Ohm Range, 0.1% and 0.5% Tolerance,
0603 Size, 0.063 W, Metal Film
Thermosensitive Chip Resis

Tolerance, 0603 Size, 0.063 W, Metal Film
Thermosensitive Chip Resistor, 0.56 Ohm to
10k Ohm Range, 5% Tolerance, 0603 Size,

Thermosensitive Chip Resistor, 0

Ohm to 1M Ohm Range, 0.1% and 0.5%
Tolerance, 0805 Size, 0.1 W

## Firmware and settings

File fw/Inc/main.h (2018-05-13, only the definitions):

#define ULINK_DEBUGGER  			2			// uncoment if swdio and swclk line used by debugger
#define EE_BUFFER_SIZE				16			// reserved RAM buffer for eeprom related operation
#define EE_TIMEOUT     				20			// 20 ms eeprom operation timeout
#define EE_BLOCK_SIZE				256			// max. byte number in one block for single write operation
#define EE_READ  					0xaf		// command to read page 0 from i2c eeprom
#define EE_WRITE 					0xae		// command to write page 0 in i2c eeprom
#define EE_PAGE_SIZE				0x10000		// 64 kByte eeprom page size
#define EE_PAGE_COUNT				512			// number of pages
#define EE_WRITE_DELAY				10			// 10 ms delay to complete write operation
#define EE_TRIALS					100			// number of i2c operation trials
#define EE_NTC_BYPASS_VOLTAGE_ADDRESS				0x00
#define EE_NTC_OPEN_VOLTAGE_ADDRESS					0x02
#define EE_NTC_WARNING_TEMPERATURE_ADDRESS			0x04
#define EE_NTC_SHUTDOWN_TEMPERATURE_ADDRESS			0x06
#define EE_SUPPLY_VOLTAGE_SHUTDOWN_ADDRESS			0x08
#define EE_PWM_0_15_FREQUENCY_ADDRESS				0x10
#define EE_PWM_16_31_FREQUENCY_ADDRESS				0x12
#define EE_RS485_INTERFACE_ADDRESS					0x20
#define EE_RS485_GROUP_ADDRESS						0x22
#define EE_RS485_BROADCAST_ADDRESS					0x24
#define EE_RS485_BAUDRATE_ADDRESS					0x26
#define EE_HC12_BAUDRATE_ADDRESS					0x30
#define EE_HC12_CHANEL_ADDRESS						0x31
#define EE_HC12_LINK_TIMEOUT_ADDRESS				0x32
#define EE_NRF24L01_BAUDRATE_ADDRESS				0x40
#define EE_NRF24L01_CHANEL_ADDRESS					0x41
#define EE_NRF24L01_LINK_TIMEOUT_ADDRESS			0x42
#define EE_NRF905_BAUDRATE_ADDRESS					0x50
#define EE_NRF905_BAND_ADDRESS						0x51
#define EE_NRF905_CHANEL_ADDRESS					0x52
#define EE_NRF905_LINK_TIMEOUT_ADDRESS				0x53

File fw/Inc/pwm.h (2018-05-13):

/**
 ******************************************************************************
 * File Name          : pwm.c
 * Date               : 04/01/2018 5:24:19
 * Description        : pwm ouput processing header
 ******************************************************************************
 *
 *
 ******************************************************************************
 */
 
/* Define to prevent recursive inclusion -------------------------------------*/
#ifndef __PWM_H
#define __PWM_H
 
 
/* Includes ------------------------------------------------------------------*/
#include "stm32f1xx.h"


/* Typedef -------------------------------------------------------------------*/
typedef enum
{
	PWM_INIT		= 0x00,
	PWM_STOP		= 0x01,
	PWM_UPDATE		= 0x02
	
} PWM_ServiceStateTypeDef;



/* Define --------------------------------------------------------------------*/
#define PWM_0_15_FREQUENCY_DEFAULT			1000		// i2c pwm controller 1 default frequency in Hertz 
#define PWM_16_31_FREQUENCY_DEFAULT			1000		// i2c pwm controller 2 default frequency in Hertz 
#define PCA9685_REGISTER_SIZE				256			// nuber of pca9685 registers
#define PWM_BUFFER_SIZE						16			// number of pwm output
#define PWM_UPDATE_TIMEOUT					12			// 20 ms pwm data transfer timeout
#define PWM_REFRESH_TIME					23			// update pwm output every 23 ms
#define PWM_NUMBER_OF_TRIAL					34			// try max. 50 times to accomplish pca9685 operation
#define PWM_ZERO_TRESHOLD					8			// +/- zero treshold to start pwm
#define PWM_DEFAULT_PRESCALE				0x1e		// prescale value for 200Hz default pwm frequncy
#define PWM_0_15_I2C_READ_ADDRESS			0x91		// pca9685 i2c bus address
#define PWM_0_15_I2C_WRITE_ADDRESS			0x90	
#define PWM_16_31_I2C_READ_ADDRESS			0x93	
#define PWM_16_31_I2C_WRITE_ADDRESS			0x92	
#define PCA9685_GENERAL_CALL_ACK			0x00		// pca9685 general call address with ACK response
#define PCA9685_GENERAL_CALL_NOACK			0x01		// pca9685 general call address without ACK response
#define PCA9685_DEFAULT_ALLCALLADR			0xe0		// pca9685 default all device call address
#define PCA9685_DEFAULT_SUBADR_1			0xe2		// pca9685 default subaddress 1
#define PCA9685_DEFAULT_SUBADR_2			0xe4		// pca9685 default subaddress 2
#define PCA9685_DEFAULT_SUBADR_3			0xe2		// pca9685 default subaddress 3
#define PCA9685_SW_RESET_COMMAND			0x06		// i2c pwm controller reset command


/* Variable ------------------------------------------------------------------*/
extern uint16_t pwm_0_15_freq;
extern uint16_t pwm_16_31_freq;
extern volatile uint32_t pwm_flags;
extern volatile uint32_t pwm_timer;
extern uint8_t pwm[PWM_BUFFER_SIZE];
extern uint8_t pca9685_register[PCA9685_REGISTER_SIZE];
extern PWM_ServiceStateTypeDef PWM_ServiceState;


//
/** ==========================================================================*/
/**    	 P C A 9 6 8 5    	R E G I S T E R  		A D D R E S S E	  		  */
/** ==========================================================================*/
//
#define PCA9685_MODE_1_REG_ADDRESS				0x00
#define PCA9685_MODE_1_RESTART_BIT				(1 << 7)
#define PCA9685_MODE_1_EXTCLK_BIT				(1 << 6)
#define PCA9685_MODE_1_AI_BIT					(1 << 5)
#define PCA9685_MODE_1_SLEEP_BIT				(1 << 4)
#define PCA9685_MODE_1_SUB_1_BIT				(1 << 3)
#define PCA9685_MODE_1_SUB_2_BIT				(1 << 2)
#define PCA9685_MODE_1_SUB_3_BIT				(1 << 1)
#define PCA9685_MODE_1_ALLCALL_BIT				(1 << 0)
#define PCA9685_MODE_2_REG_ADDRESS				0x01
#define PCA9685_MODE_2_INVRT_BIT				(1 << 4)
#define PCA9685_MODE_2_OCH_BIT					(1 << 3)
#define PCA9685_MODE_2_OUTDRV_BIT				(1 << 2)
#define PCA9685_MODE_2_OUTNE_1_BIT				(1 << 1)
#define PCA9685_MODE_2_OUTNE_0_BIT				(1 << 0)
#define PCA9685_SUBADR_1_REG_ADDRESS			0x02
#define PCA9685_SUBADR_2_REG_ADDRESS			0x03
#define PCA9685_SUBADR_3_REG_ADDRESS			0x04
#define PCA9685_ALLCALLADR_REG_ADDRESS			0x05
#define PCA9685_LED_0_ON_L_REG_ADDRESS			0x06
#define PCA9685_LED_0_ON_H_REG_ADDRESS			0x07
#define PCA9685_LED_0_OFF_L_REG_ADDRESS			0x08
#define PCA9685_LED_0_OFF_H_REG_ADDRESS			0x09
#define PCA9685_LED_1_ON_L_REG_ADDRESS			0x0a
#define PCA9685_LED_1_ON_H_REG_ADDRESS			0x0b
#define PCA9685_LED_1_OFF_L_REG_ADDRESS			0x0c
#define PCA9685_LED_1_OFF_H_REG_ADDRESS			0x0d
#define PCA9685_LED_2_ON_L_REG_ADDRESS			0x0e
#define PCA9685_LED_2_ON_H_REG_ADDRESS			0x0f
#define PCA9685_LED_2_OFF_L_REG_ADDRESS			0x10
#define PCA9685_LED_2_OFF_H_REG_ADDRESS			0x11
#define PCA9685_LED_3_ON_L_REG_ADDRESS			0x12
#define PCA9685_LED_3_ON_H_REG_ADDRESS			0x13
#define PCA9685_LED_3_OFF_L_REG_ADDRESS			0x14
#define PCA9685_LED_3_OFF_H_REG_ADDRESS			0x15
#define PCA9685_LED_4_ON_L_REG_ADDRESS			0x16
#define PCA9685_LED_4_ON_H_REG_ADDRESS			0x17
#define PCA9685_LED_4_OFF_L_REG_ADDRESS			0x18
#define PCA9685_LED_4_OFF_H_REG_ADDRESS			0x19
#define PCA9685_LED_5_ON_L_REG_ADDRESS			0x1a
#define PCA9685_LED_5_ON_H_REG_ADDRESS			0x1b
#define PCA9685_LED_5_OFF_L_REG_ADDRESS			0x1c
#define PCA9685_LED_5_OFF_H_REG_ADDRESS			0x1d
#define PCA9685_LED_6_ON_L_REG_ADDRESS			0x1e
#define PCA9685_LED_6_ON_H_REG_ADDRESS			0x1f
#define PCA9685_LED_6_OFF_L_REG_ADDRESS			0x20
#define PCA9685_LED_6_OFF_H_REG_ADDRESS			0x21
#define PCA9685_LED_7_ON_L_REG_ADDRESS			0x22
#define PCA9685_LED_7_ON_H_REG_ADDRESS			0x23
#define PCA9685_LED_7_OFF_L_REG_ADDRESS			0x24
#define PCA9685_LED_7_OFF_H_REG_ADDRESS			0x25
#define PCA9685_LED_8_ON_L_REG_ADDRESS			0x26
#define PCA9685_LED_8_ON_H_REG_ADDRESS			0x27
#define PCA9685_LED_8_OFF_L_REG_ADDRESS			0x28
#define PCA9685_LED_8_OFF_H_REG_ADDRESS			0x29
#define PCA9685_LED_9_ON_L_REG_ADDRESS			0x2a
#define PCA9685_LED_9_ON_H_REG_ADDRESS			0x2b
#define PCA9685_LED_9_OFF_L_REG_ADDRESS			0x2c
#define PCA9685_LED_9_OFF_H_REG_ADDRESS			0x2d
#define PCA9685_LED_10_ON_L_REG_ADDRESS			0x2e
#define PCA9685_LED_10_ON_H_REG_ADDRESS			0x2e
#define PCA9685_LED_10_OFF_L_REG_ADDRESS		0x30
#define PCA9685_LED_10_OFF_H_REG_ADDRESS		0x31
#define PCA9685_LED_11_ON_L_REG_ADDRESS			0x32
#define PCA9685_LED_11_ON_H_REG_ADDRESS			0x33
#define PCA9685_LED_11_OFF_L_REG_ADDRESS		0x34
#define PCA9685_LED_11_OFF_H_REG_ADDRESS		0x35
#define PCA9685_LED_12_ON_L_REG_ADDRESS			0x36
#define PCA9685_LED_12_ON_H_REG_ADDRESS			0x37
#define PCA9685_LED_12_OFF_L_REG_ADDRESS		0x38
#define PCA9685_LED_12_OFF_H_REG_ADDRESS		0x39
#define PCA9685_LED_13_ON_L_REG_ADDRESS			0x3a
#define PCA9685_LED_13_ON_H_REG_ADDRESS			0x3b
#define PCA9685_LED_13_OFF_L_REG_ADDRESS		0x3c
#define PCA9685_LED_13_OFF_H_REG_ADDRESS		0x3d
#define PCA9685_LED_14_ON_L_REG_ADDRESS			0x3e
#define PCA9685_LED_14_ON_H_REG_ADDRESS			0x3f
#define PCA9685_LED_14_OFF_L_REG_ADDRESS		0x40
#define PCA9685_LED_14_OFF_H_REG_ADDRESS		0x41
#define PCA9685_LED_15_ON_L_REG_ADDRESS			0x42
#define PCA9685_LED_15_ON_H_REG_ADDRESS			0x43
#define PCA9685_LED_15_OFF_L_REG_ADDRESS		0x44
#define PCA9685_LED_15_OFF_H_REG_ADDRESS		0x45
/**
*	Reserved addresse for future use
*/
#define PCA9685_ALL_LED_ON_L_REG_ADDRESS		0xfa
#define PCA9685_ALL_LED_ON_H_REG_ADDRESS		0xfb
#define PCA9685_ALL_LED_OFF_L_REG_ADDRESS		0xfc
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

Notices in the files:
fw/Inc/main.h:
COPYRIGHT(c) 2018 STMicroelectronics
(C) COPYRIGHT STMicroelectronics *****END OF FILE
